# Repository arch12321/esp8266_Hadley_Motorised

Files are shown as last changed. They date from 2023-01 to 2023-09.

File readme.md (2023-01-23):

# Intro

***PLEASE NOTE MAIN VERSIONS OF MODELS AND CODE EXIST ON GITHUB ALONG WITH THE CODE AND WILL DO SO UNTIL PRINTABLES SUPPORTS PULL REQUESTS***

Welcome to my update to the metric hadley to add motorised control.  Please note that as the code (initialy VERY basic) evolves it will live on GitHub where folk who are way smarter and talented than me hopefully will make it better.  Similarly the models will exist on GitHub so that folk can improve and merge change their improvements to a single place so that there is a hopefully single best version (hopefully) and not many forks.

Once build, this will allow you to control your telescope from a webpage.   In due course the intent is to improve the code so that you can select targets and the telescope automatically moves to point at it, and will track it's position over time.  This requires a few more updates, and some coding to make work, but it's very possible.

With this, I recommend replacing the all plastic bearings with ‘proper’ bearings, this gives much smoother movement.  While it will work without this, the movement can be slightly jerky which would be a problem for small/slow movements when tracking objects in the sky.  

Anyway - firstly - the readme on github is the latest doc - pls see that for more details and code etc.

# Parts list

For hardware that needs to be purchased, you will need:

* ESP8266 Microcontroller (I used a D1 mini clone) - something like https://www.amazon.co.uk/dp/B08BTH77F3 (note, in theory you could use an ESP32, the code should be compatible, however I haven't tested it with an ESP32, so it almost certainly won't work without some bug fixing first)
* Lazy Susan Bearing - I used this one (140mm), and all the holes etc. are based this - I have no idea how standard they are - https://www.amazon.co.uk/gp/product/B00TQT9U7U/ 
* A4988 stepper motor drivers (https://www.amazon.co.uk/gp/product/B07MXXL2KW/) note - you can use the standard ULN2003 drivers, you will just need to make a couple of code tweaks and will get less torque.  The changes are commented out in the source code.  NB - I got HR4988 chips, not A4988 - these seem to work fine and I think are just cheap chinese rip offs of the real thing, so I wouldn't expect huge longevity, but so far they seem to work.
* 2 x 28BYJ-48 5V stepper motors ( https://www.amazon.co.uk/dp/B07PPKS7GZ/ ) - I had some lying around I think I got from aliexpress for about $1 each, they seem pretty universal though. Just get the 5V version
* An electrolytic capacitor (at least 100uF and >12V).  I think mine is 1000uF, but that's too big, it's just one I had a drawer full of
* 5V → 12V boost converter (10V would prob be OK too).  I used this https://www.amazon.co.uk/gp/product/B08M42BT3G/ but anything that can 0.4 A at 12V should be plenty (I measure about 95mA per motor, I have no idea how much the stepper controllers use, but they get hot..so some..) so I would estimate a total of 400mA capacity should give plenty of headroom
* 2 x 6700 bearings (2RS, ZZ - doesn't matter)
* Some solder, basic soldering skills
* A computer to flash the ESP8266 (i.e to load the computer program onto the ESP8266 microcontroller)
* USB battery pack and micro-USB wire for power
* 6mm wide closed loop GT2 timing belt - I used a 500mm one, but I think a 400mm would be OK
* 8mm M4 screws x4 (I think)
* 4 x M4 nuts
* 12mm M4 screws x16 (I think - You can get away with 8mm screws for these if needed - 8 of these hold the modified bearings (large semicircular ish things) in place - I ran out and used 8mm screws here - they are OK but 12mm better)
* 8mm M3 screws x6 (to secure the motors and bearings)
* 6mm M3 Heat set inserts x6
* 6mm M4 Heat set inserts x 12 (could use 8 here - 8 of these these connect the metric frame to the rotating base, I used 4 due to me being tighter than 2 layers of paint, there are holes for 8).  The other 4 are for the below screws.
* 16mm M4 x4 (these go through the lazy susan from the bottom into heat set inserts to hold the rotation base (the thing that deliberately looks a bit like a ship's helm) to the bearing)
* 10mm M4 Heat set inserts (could use a different size) x4.  These are to hold the bearing and ring gear to the optional base.
* Countersunk 20mm M4 screws - these connect the lazy susan to the optional base

# Circuit design

This is pretty straight forward, I just used some stripboard (approx 60mm x 60mm in size) and soldered together some breakout boards.  I wanted to have it so I could power the whole thing from a USB power bank as turny things connected to wires leads to tangles, so having an isolated power source I could put inside the turny thing seemed sensible and to provide the 5V input to drive the esp8266 board.  I therefore used a boost converter to get the required 12v ish to drive the motor (more on why I need 12V to drive 5V motors below) all powered from a 5V input.

While I haven't actually drawn the circuit properly - I have put some photos of the way I did it.  Note you probably could power this direct from the ESP8266 micro USB, I just just the separate board to put the power input in a different place.

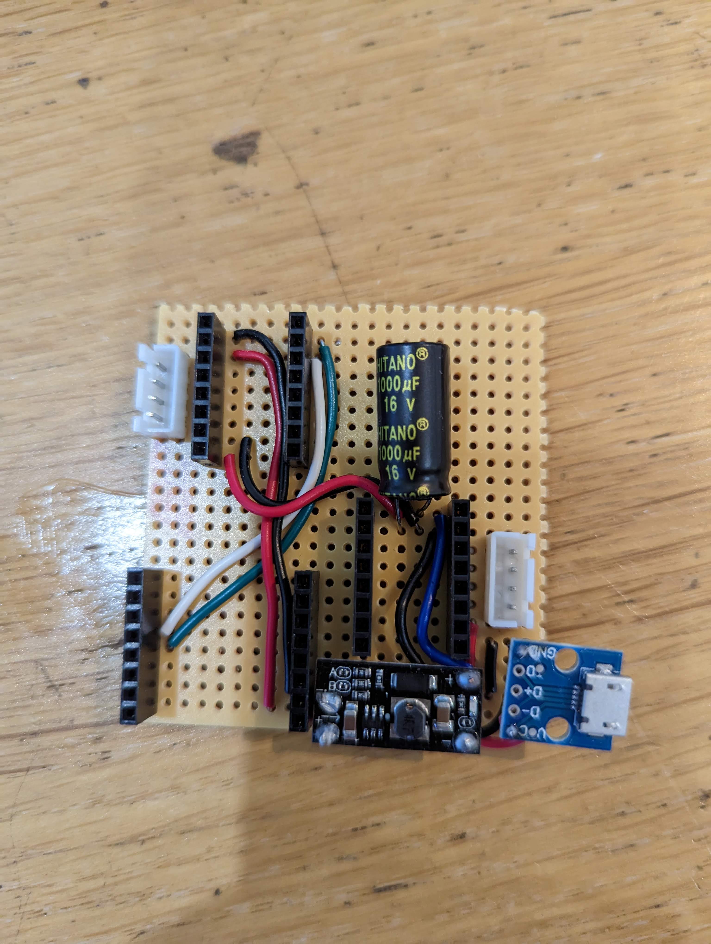
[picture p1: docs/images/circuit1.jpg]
photo of circuit1

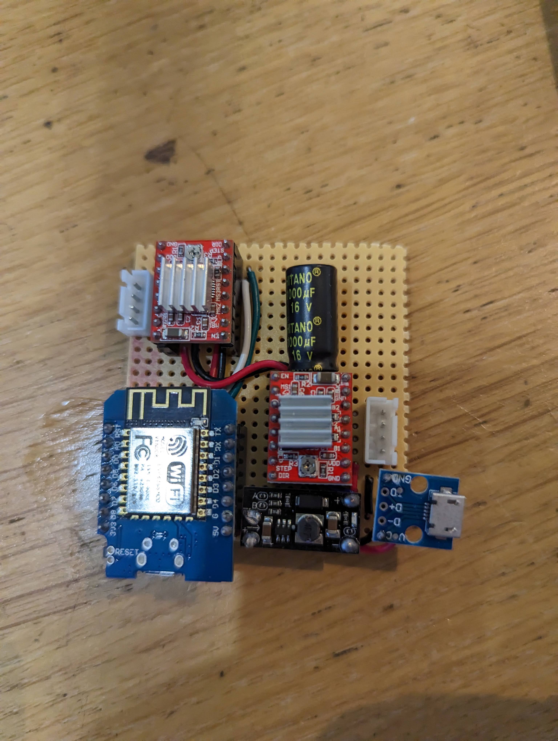
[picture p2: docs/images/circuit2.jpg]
photo of circuit2

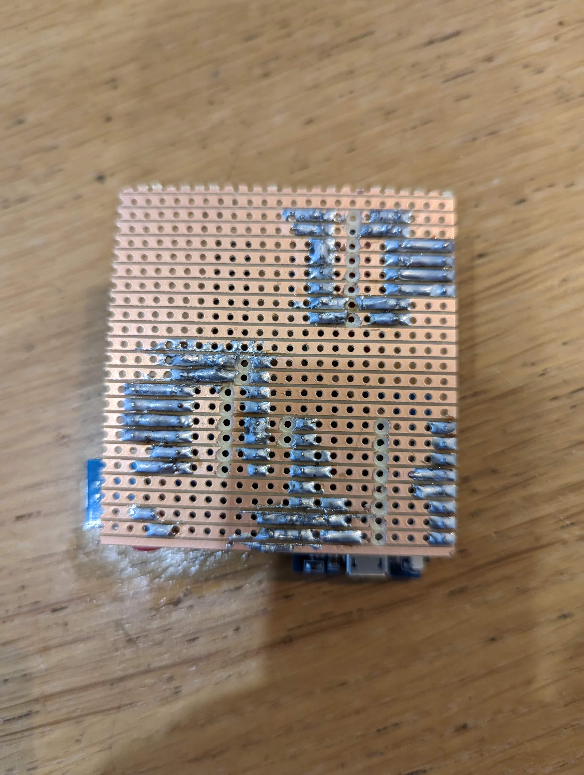
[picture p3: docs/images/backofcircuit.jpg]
photo of backofcircuit


# Stepper Driver Setup

You can use the ULN2003 driver for the 28BYJ-48 stepper motor with no modifications in unipolar mode, however various folks have noted this gives a torque of around 300-380g.cm of torque - this can be roughly doubled to 800g.cm by moving to bipolar operation (which as you move from energising 1/4 of the coils at one time in unipolar mode to energising 1/2 the coils at one time kinda makes empirical sense to me).  From my experiements, moving the steppers to bipolar operation did indeed improve performance, and while the steppers in unipolar/ULN2003 operation do move the telescope, more torque is more reliable, less likely to miss steps, and as Mr Clarkson might say, more power = better.  Given the simplicity of the modification and low cost of A4988 boards (mine are actually HR4988 boards due to dubious sales tactics calling them A4988 compatible (I missed the compatible bit) but they work fine) I decided to go for bipolar operation in this.  See https://ardufocus.com/howto/28byj-48-bipolar-hw-mod/ for details on how to do this.  The one problem I ran into was that when removing the blue plastic cover to access the PCB, a bit of the blue plastic broke off and stayed in the housing, which given there are small white plastic gears in the same area seems less than ideal.  The motor that controls elevation (up/down) is orientated such that if there is a small bit of plastic it should sit away from the plastic gears and so be OK (the gears are only one side of the motor). This however won't work for the motor that rotates the telescope, and so in one of the photos on https://www.printables.com/model/377199-motorised-mount-for-hadley-telescope oif the motor showing the motor PCB you will see I bent the side of the housing out - this was to get that super annoying bit of blue plastic out - this is easy to do with needle nosed pliars.

From the photos you will see I also removed the red wire and replaced the 5 pin JST connector with a 4 pin JST conector and sleeved the cables with white PET sleeving.  This is entirely optional and I did it both to simplify the connections to the stepper driver board, and also to assuage some of my OCD by making it look tidier overall.  The remaining niggle is I only had white sleeving, and everything else is black, which annoys me, but I think I can live with it...I think...In any case, should you decide to replace the JST connector, I recommend cutting the 5 pin plastic JST housing off the pins rather than either trying to remove the pins individually or cutting the wires and crimping on new connectors.  Having tried all 3 approaches, destroying the white plastic JST housing I found far and away the quickest and easiest approach.

The current limit of the 125mV a4988 potentiometer - gives approx 95mA measured at full step.  Equates to current limit of (1/0.7)*95 = 136mA limit as full step current is limited to 70% of max.

Note need at LEAST 47uF (I would use a min of 100uF) electrolytic capacitor to protect a4988 board from LSC voltage spikes. See https://www.pololu.com/docs/0J16/all for more details on this fascinating topic.  TL:DR? Do not use a ceramic capacitor.

# Mechanical Gearing

Note the conversion of degrees to number of steps is done in the JS file.  This is done to decouple essentially config from the ESP8266 firmware.  In due course, the intent is separate the HTML/JS/CSS files from hosting on the ESP8266 to decouple this and accelerate development, though frankly OTA updates are not hard so whether this ever gets done is low priority, especially as it's possible to update the filesystem and code over the air (OTA) over a local network.

## Horizontal
Ring gear = 82 teeth<br>
Drive gear = 10 teeth<br>
Stepper motor =-= 32*63.68395 steps per revolution = 2037.8864<br>

Therefore full revolution = (82/10)*2037.8864 = 16,710.66848 steps per 360 degrees<br>
And 1 degree = 46.41852355555556 steps<br>
Or 1 step = 0.0215431238092517 degrees<br>

https://randomnerdtutorials.com/stepper-motor-esp32-websocket/<br>

## Vertical
Big wheel 150 teeth upped to 230<br>
Drive wheel 20 teeth - (small version 12)<br>

Therefore full revolution = (230/20)*2037.8864 = 16,710.66848 steps per 360 degrees<br>
And 1 degree = 65.0991488888889 steps<br>
Or 1 step = 0.015361183933553 degrees<br>

## Summary

| Item | Turntable | Elevation |
| ---- | ---- | ---- |
| Drive Gear | 10 | 20 |
| Pulley | 82 | 230 |
| Mechanical Advantage | 8.2 | 11.5 |
| Steps per revolution (motor) | 2037.8864 | 2037.8864 |
| Steps per revolution (telescope) | 16710.66848 | 23435.6936 |
| No. of steps to move 1 degree | 46.41852356 | 65.09914889 |
| No of degrees 1 step moves | 0.021543124 | 0.015361184 |

# Flashing ESP8266 (i.e. putting the code onto the ESP8266)

If you are not familiar with flashing microcontroller, I highly recommend the Random Nerds tutorials.  This repo uses VS Code running PlatformIO, and I recommend this is what you use to flash - there is a full guide here: https://randomnerdtutorials.com/vs-code-platformio-ide-esp32-esp8266-arduino/ on how to set everything up - this can be daunting at first, but if you follow the guide, you should be fine.  Once you have VS Code setup and PlatformIO installed in VS Code just follow the steps below:

1. Clone the github repo or download the code and unzip to folder.  You should now have a folder with all the code in multiple folders and few files in the top level directory (e.g. readme.md, platformio.ini and some others)
2. Open VS Code, go to File --> Open Folder and find the folder you unzipped the files into (this folder must contain platformio.ini at the top level within it - not another folder with the platformio.ini in that)
3. Plug your ESP8266 into computer (if using an ESP32, update the platformio.ini file with your board, platform, and remove the filesystem line as you'll use SPIFFS not LITTLEFS)
4. Click the alien head in the left hand menu (platformio icon) and click Platform --> Erase Flash (just to be sure) and wait for a success message in the terminal.  Should take 15-20 seconds ish.
5. In theame menu, click Platform --> Build Filesystem Image and wait for a success message in the terminal. Should take a few seconds.
6. In the same menu, click Platform --> Upload Filesystem Image and wait for a success message in the terminal.  These steps, wipe the flash memory, then uploads the HTML, CSS and JS files in the "data" folder to the microcontroller.  Should take 10-15 seconds.
7. Click the right pointing arrow at the bottom of your screen (or click the alien head in the left hand menu --> General --> upload).  This will compile the code and then upload the binary to your microcontroller, then reset it.  This should take around 40-50 seconds.  If you now click the 2 pronged plug thing at the bottom of your screen you should get the serial messages from the microcontroller.
8. With your phone/laptop/computer/tablet open your wifi settings, and connect to the HadleyTelescope wifi network
9. If not autodirected, go to the sign-in page (192.168.4.1 by default) and click on "Configuration".  In the fist SSID box, put your wifi network name and the password in the Password field. Leave the rest blank or with default values.  Click "SAVE"
10. If you clicked the 2 pronged plug icon thing at the bottom of your screen (serial monitor terminal) you should then see a bunch more info and the local IP of your microcontroller.  If not, you can probably find it with the hostname of [http://hadleyTelescope](http://hadleyTelescope) or in your router's DHCP tables.  If you didn't click the 2 pronged plug - you can do so now, and click the reset button on your microcontroller (or unplug and plug back it back in) and you can get the local IP address.

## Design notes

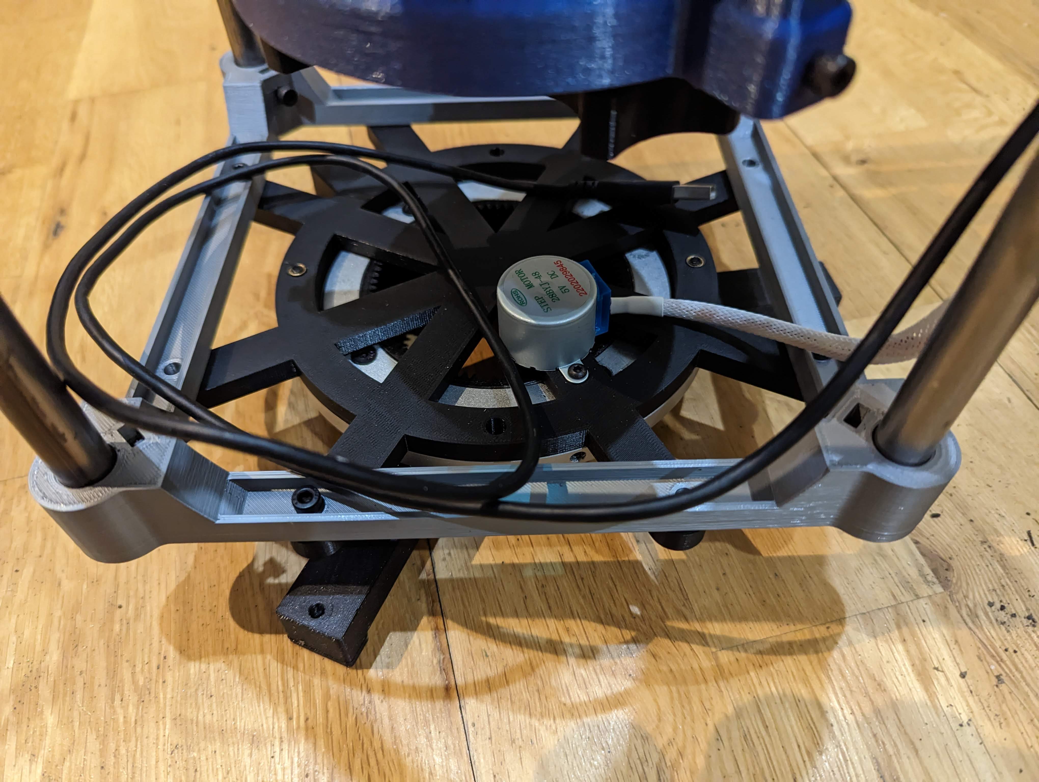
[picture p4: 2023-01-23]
docs/images/base.jpg

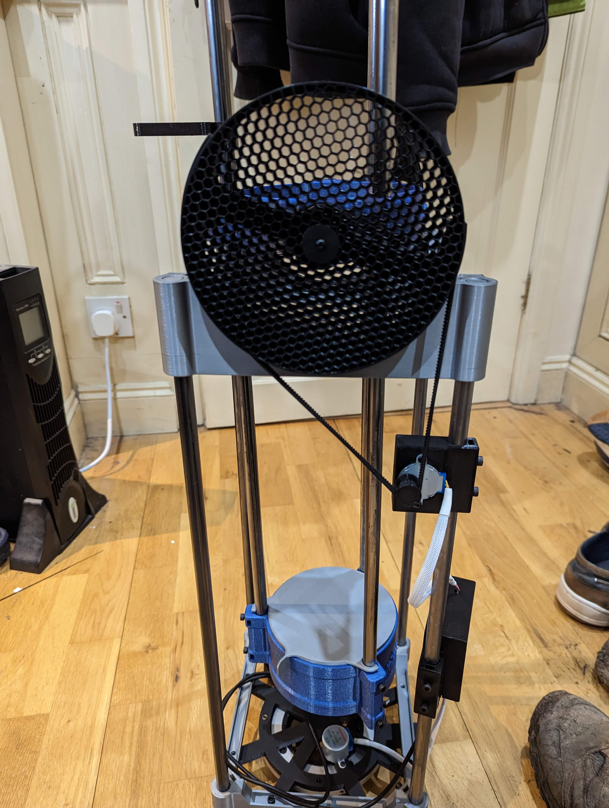
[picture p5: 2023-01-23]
docs/images/telescope.jpg

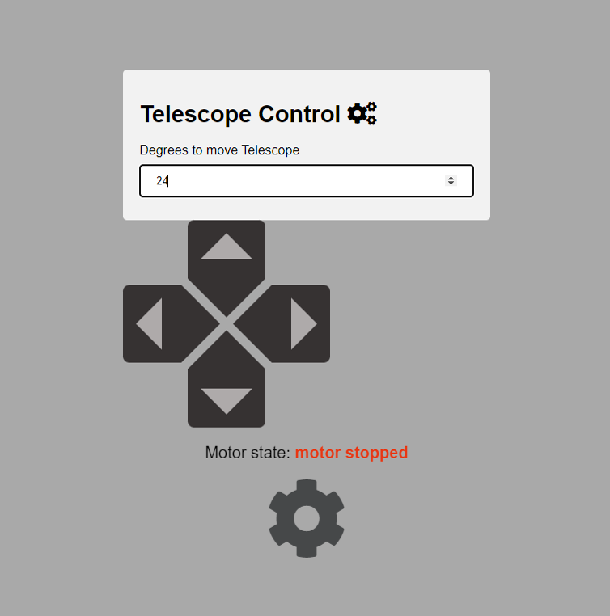
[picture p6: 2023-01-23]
docs/images/ui.png

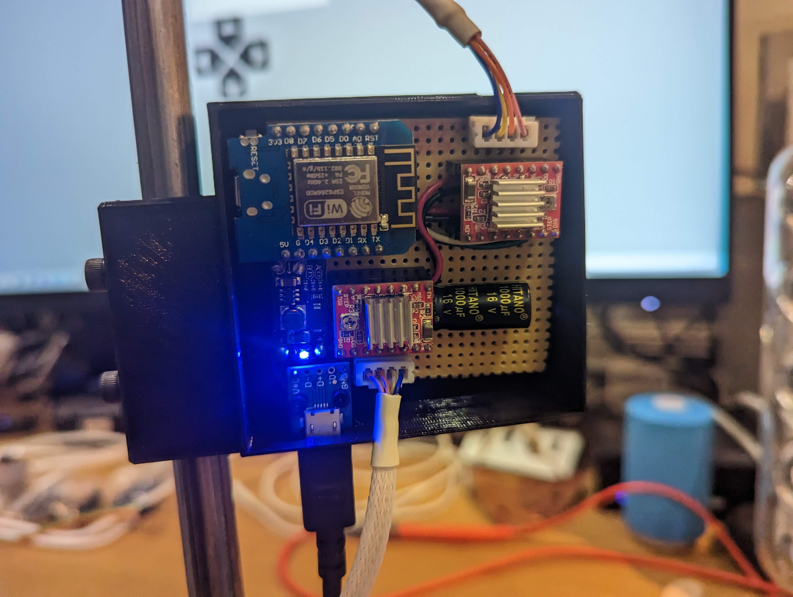
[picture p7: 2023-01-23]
docs/images/circuitinabox.jpg

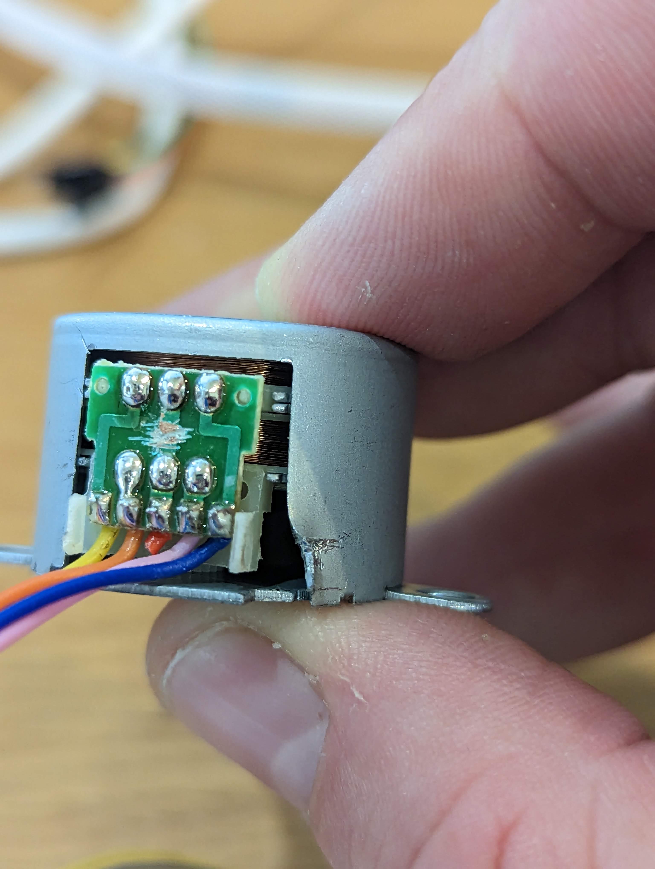
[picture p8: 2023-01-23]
docs/images/bipolarmod.jpg

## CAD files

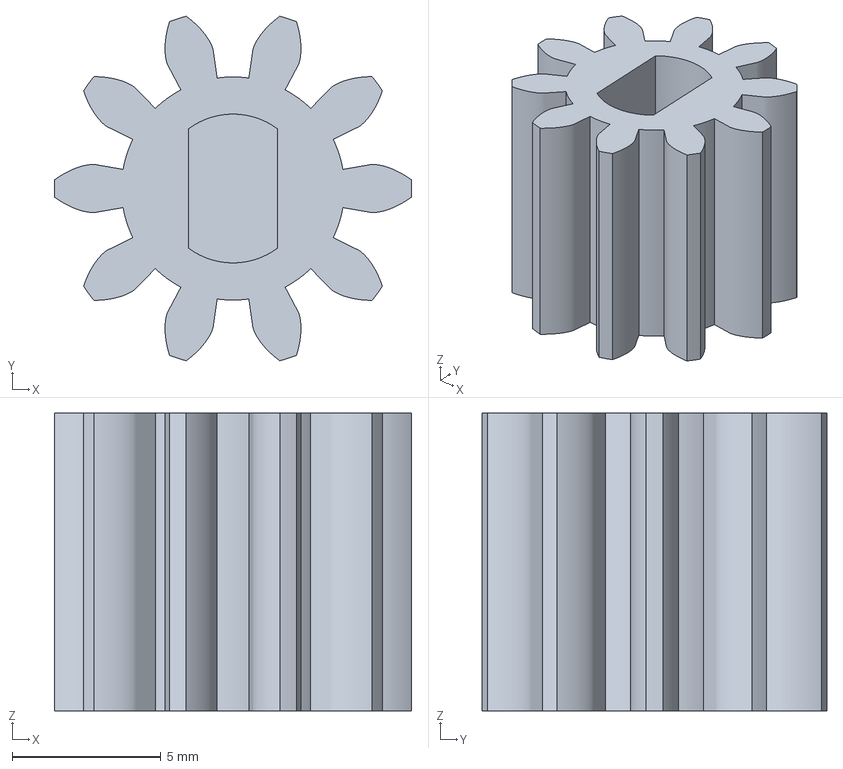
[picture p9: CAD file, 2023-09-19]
docs/10 tooth spur.3mf
12.0 x 11.6 x 10.0 mm

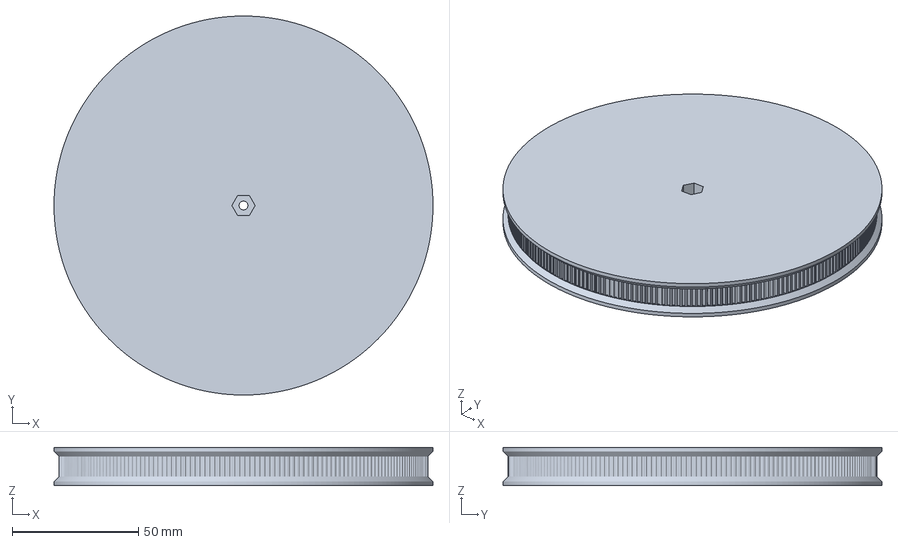
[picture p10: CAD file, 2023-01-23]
docs/Bearing mount pulley large.3mf
149.9 x 149.9 x 15.2 mm

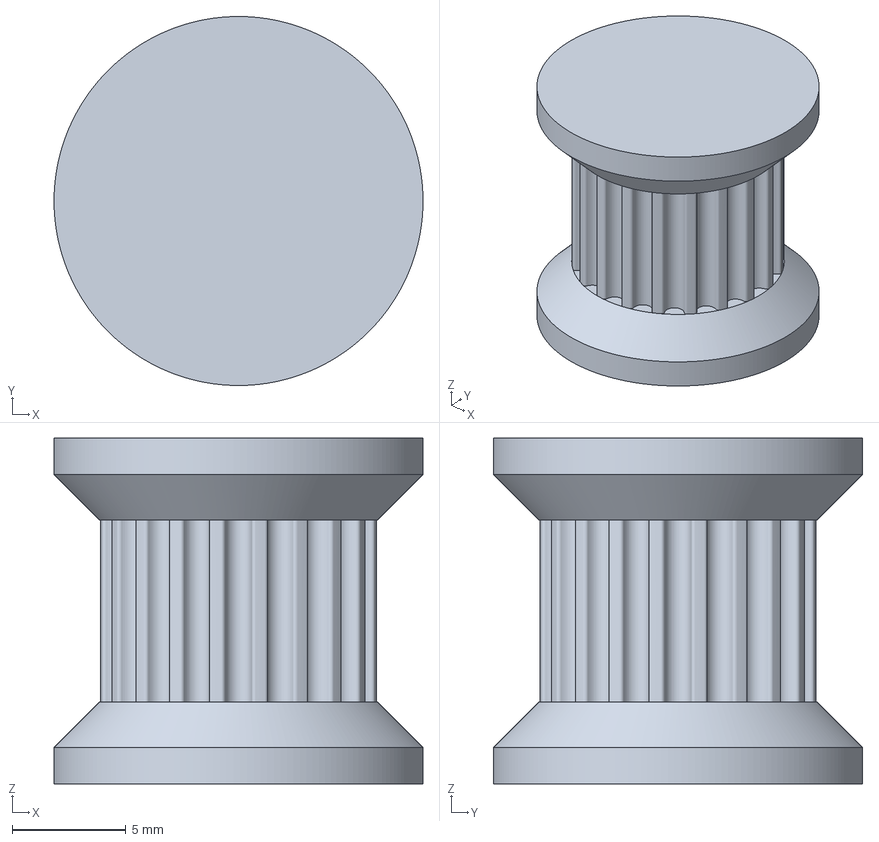
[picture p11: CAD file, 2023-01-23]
docs/GT2 drive gear.3mf
16.2 x 16.2 x 15.2 mm

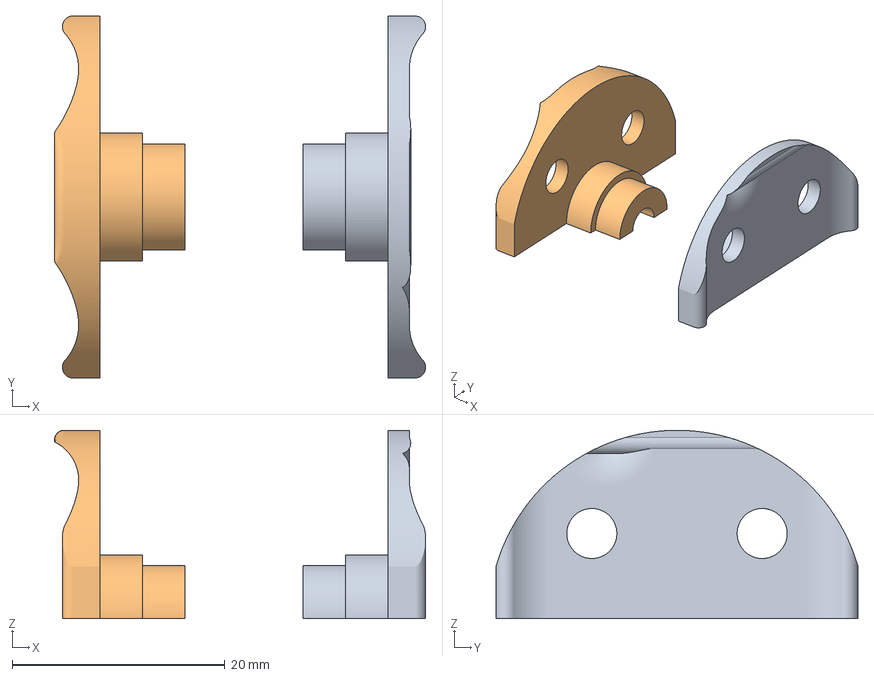
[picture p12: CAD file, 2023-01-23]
docs/Bearing Mounts - no pulley.3mf
34.9 x 34.0 x 17.7 mm
Bearing Mount 2
Bearing Mount 1

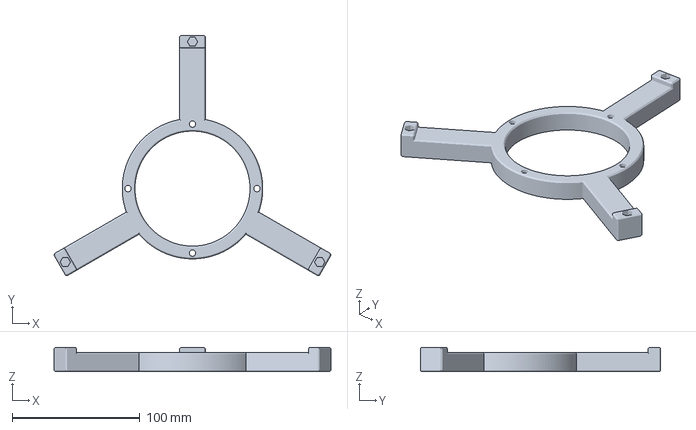
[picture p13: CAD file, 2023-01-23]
docs/base.3mf
216.8 x 188.2 x 19.0 mm

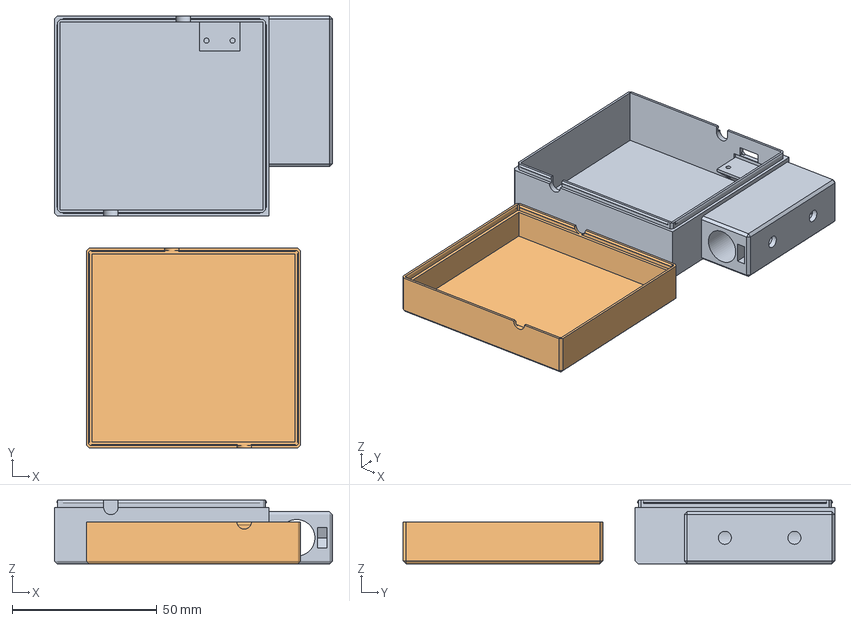
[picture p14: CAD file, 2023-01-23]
docs/electronics box v2.3mf
96.0 x 149.1 x 22.0 mm
pulley mount v6.stl_2
Electronics Box Top v2.stl

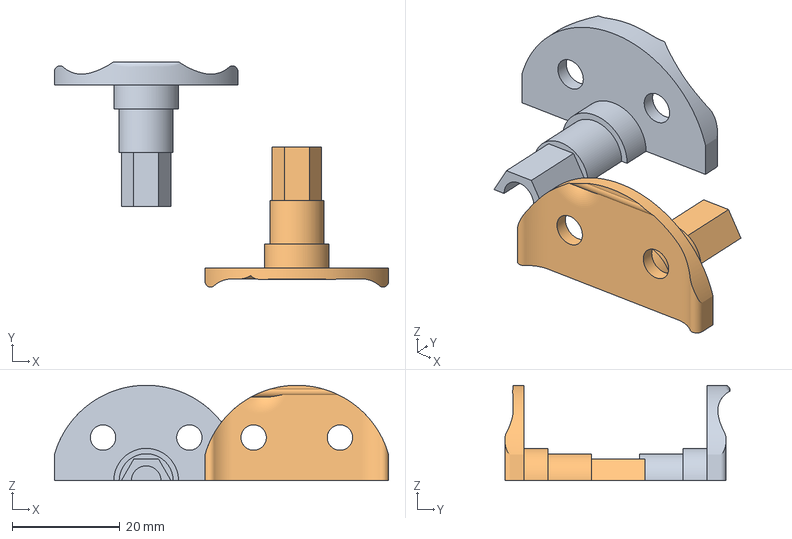
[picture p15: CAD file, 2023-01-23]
docs/Bearing Mounts.3mf
61.9 x 41.8 x 17.7 mm
Bearing Mount 1
Bearing Mount 2

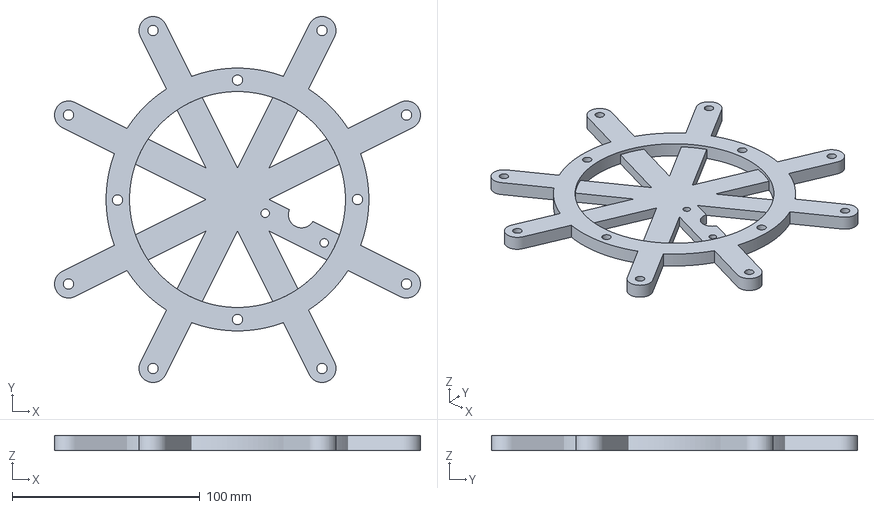
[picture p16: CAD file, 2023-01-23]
docs/rotation base.3mf
195.0 x 195.0 x 8.00 mm

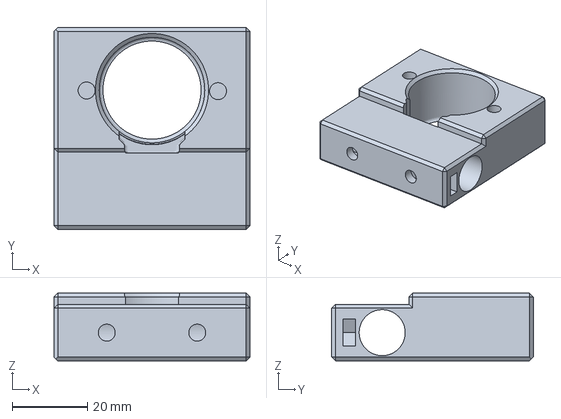
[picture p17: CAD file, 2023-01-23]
docs/Motor vertical mount.3mf
52.0 x 53.5 x 18.0 mm

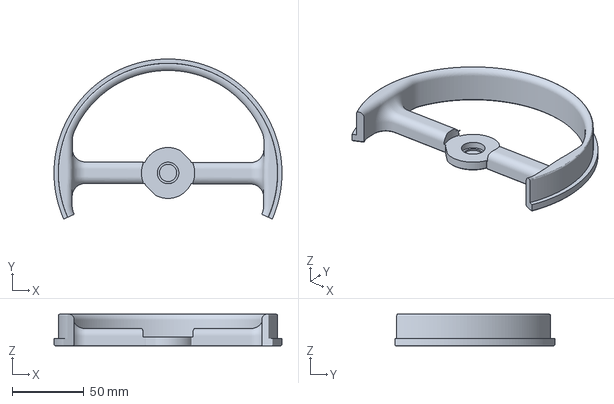
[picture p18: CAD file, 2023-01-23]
docs/Bearing mount np pulley large.3mf
158.4 x 111.1 x 22.0 mm

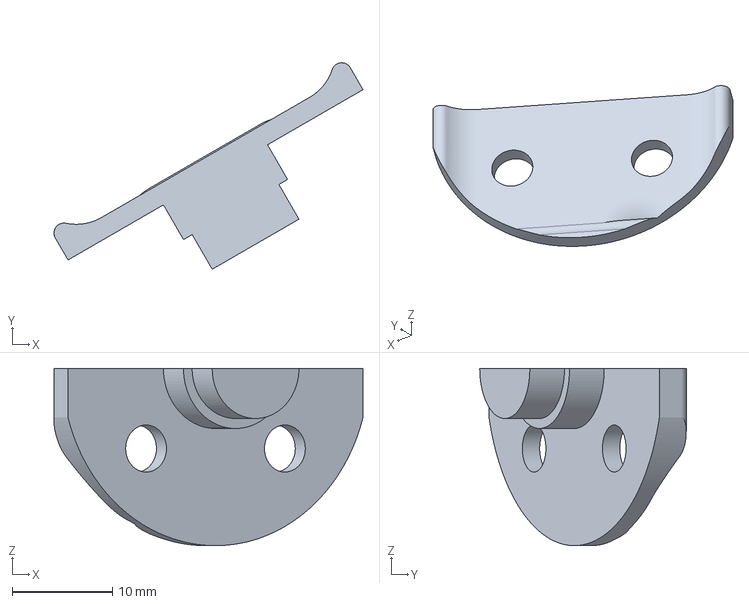
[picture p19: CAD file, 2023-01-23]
docs/Bearing Mount 2 - no pulley.3mf
30.8 x 20.6 x 17.7 mm

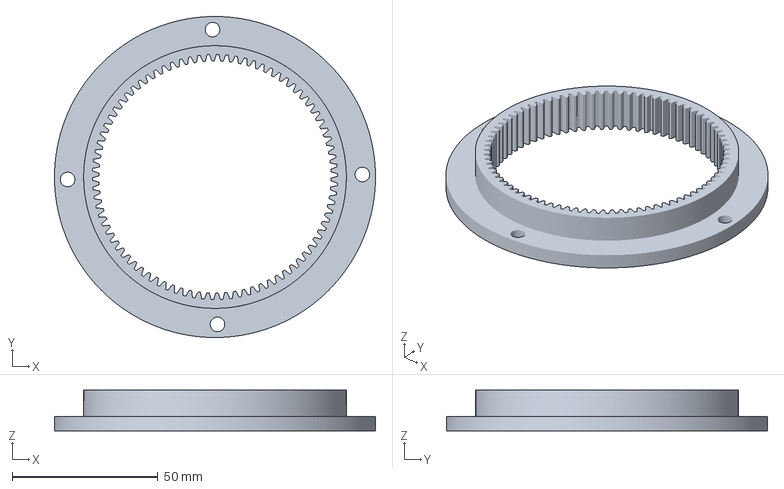
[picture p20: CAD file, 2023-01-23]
docs/Ring gear.3mf
110.0 x 110.0 x 14.0 mm

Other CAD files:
docs/Bearing for Pulley.3mf

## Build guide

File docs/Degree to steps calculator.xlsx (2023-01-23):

 | Turntable | Vertical
Drive Gear | 10 | 20
Pulley | 82 | 230
Mechanical Advantage | 8.2 | 11.5
Steps per revolution (motor) | 2037.8864 | 2037.8864
Steps per revolution (telescope) | 16710.66848 | 23435.6936
No. of steps to move 1 degree | 46.4185235556 | 65.0991488889
No of degrees 1 step moves | 0.02154312381 | 0.0153611839

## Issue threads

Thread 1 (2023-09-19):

Missing 10 tooth drive gear

Verethy-0127, 2023-09-19:
Just about got this project done, but seem to be missing the 10t drive gear for the base. Not sure if you forgot to include the STL or if this is not mentioned in the BOM?

arch12321, 2023-09-19:
Hey - thanks for building it - i have added the 10 tooth spur gear from my print files.  Pls let me know how you get on!

Closed 2023-09-19.

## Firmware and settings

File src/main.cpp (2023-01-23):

/*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
    You should have received a copy of the GNU General Public License
    along with this program.  If not, see <https://www.gnu.org/licenses/>.
*/

#define ESP_ASYNC_WIFIMANAGER_VERSION_MIN_TARGET      "ESPAsync_WiFiManager v1.15.0"
#define ESP_ASYNC_WIFIMANAGER_VERSION_MIN             1015000

// Use from 0 to 4. Higher number, more debugging messages and memory usage.
#define _ESPASYNC_WIFIMGR_LOGLEVEL_    3

// To not display stored SSIDs and PWDs on Config Portal, select false. Default is true
// Even the stored Credentials are not display, just leave them all blank to reconnect and reuse the stored Credentials 
//#define DISPLAY_STORED_CREDENTIALS_IN_CP        false

//Ported to ESP32
#ifdef ESP32
  #include <esp_wifi.h>
  #include <WiFi.h>
  #include <WiFiClient.h>

  //needed for Arduino OTA
  #include <ESPmDNS.h>

  // From v1.1.1
  #include <WiFiMulti.h>
  WiFiMulti wifiMulti;

  // LittleFS has higher priority than SPIFFS
  #if ( defined(ESP_ARDUINO_VERSION_MAJOR) && (ESP_ARDUINO_VERSION_MAJOR >= 2) )
    #define USE_LITTLEFS    true
    #define USE_SPIFFS      false
  #elif defined(ARDUINO_ESP32C3_DEV)
    // For core v1.0.6-, ESP32-C3 only supporting SPIFFS and EEPROM. To use v2.0.0+ for LittleFS
    #define USE_LITTLEFS          false
    #define USE_SPIFFS            true
  #endif

  #if USE_LITTLEFS
    // Use LittleFS
    #include "FS.h"

    // Check cores/esp32/esp_arduino_version.h and cores/esp32/core_version.h
    //#if ( ESP_ARDUINO_VERSION >= ESP_ARDUINO_VERSION_VAL(2, 0, 0) )  //(ESP_ARDUINO_VERSION_MAJOR >= 2)
    #if ( defined(ESP_ARDUINO_VERSION_MAJOR) && (ESP_ARDUINO_VERSION_MAJOR >= 2) )
      #if (_ESPASYNC_WIFIMGR_LOGLEVEL_ > 3)
        #warning Using ESP32 Core 1.0.6 or 2.0.0+
      #endif
      
      // The library has been merged into esp32 core from release 1.0.6
      #include <LittleFS.h>       // https://github.com/espressif/arduino-esp32/tree/master/libraries/LittleFS
      
      FS* filesystem =      &LittleFS;
      #define FileFS        LittleFS
      #define FS_Name       "LittleFS"
    #else
      #if (_ESPASYNC_WIFIMGR_LOGLEVEL_ > 3)
        #warning Using ESP32 Core 1.0.5-. You must install LITTLEFS library
      #endif
   
      // The library has been merged into esp32 core from release 1.0.6
      #include <LITTLEFS.h>       // https://github.com/lorol/LITTLEFS
      
      FS* filesystem =      &LITTLEFS;
      #define FileFS        LITTLEFS
      #define FS_Name       "LittleFS"
    #endif
    
  #elif USE_SPIFFS
    #include <SPIFFS.h>
    FS* filesystem =      &SPIFFS;
    #define FileFS        SPIFFS
    #define FS_Name       "SPIFFS"
  #else
    // +Use FFat
    #include <FFat.h>
    FS* filesystem =      &FFat;
    #define FileFS        FFat
    #define FS_Name       "FFat"
  #endif
  //////

  #define LED_BUILTIN       2
  #define LED_ON            HIGH
  #define LED_OFF           LOW

#else

  #include <ESP8266WiFi.h>          //https://github.com/esp8266/Arduino
  //needed for library
  #include <ESPAsyncDNSServer.h>

  //needed for Arduino OTA
  #include <ESP8266mDNS.h>

  // From v1.1.1
  #include <ESP8266WiFiMulti.h>
  ESP8266WiFiMulti wifiMulti;

  #define USE_LITTLEFS      true
  
  #if USE_LITTLEFS
    #include <LittleFS.h>
    FS* filesystem =      &LittleFS;
    #define FileFS        LittleFS
    #define FS_Name       "LittleFS"
  #else
    FS* filesystem =      &SPIFFS;
    #define FileFS        SPIFFS
    #define FS_Name       "SPIFFS"
  #endif
  //////
  
  #define ESP_getChipId()   (ESP.getChipId())
  
  #define LED_ON      LOW
  #define LED_OFF     HIGH
#endif

//Telescope control generic includes
#include <Arduino.h>
#include <ESPAsyncWebServer.h>
#include <AccelStepper.h>

//ArduinoOTA generic includes
#include <WiFiUdp.h>
#include <ArduinoOTA.h>

// SSID and PW for your Router
String Router_SSID;
String Router_Pass;

// From v1.1.1
// You only need to format the filesystem once
//#define FORMAT_FILESYSTEM       true
#define FORMAT_FILESYSTEM         false

#define MIN_AP_PASSWORD_SIZE    8

#define SSID_MAX_LEN            32
//From v1.0.10, WPA2 passwords can be up to 63 characters long.
#define PASS_MAX_LEN            64

typedef struct
{
  char wifi_ssid[SSID_MAX_LEN];
  char wifi_pw  [PASS_MAX_LEN];
}  WiFi_Credentials;

typedef struct
{
  String wifi_ssid;
  String wifi_pw;
}  WiFi_Credentials_String;

#define NUM_WIFI_CREDENTIALS      2

// Assuming max 49 chars
#define TZNAME_MAX_LEN            50
#define TIMEZONE_MAX_LEN          50

typedef struct
{
  WiFi_Credentials  WiFi_Creds [NUM_WIFI_CREDENTIALS];
  char TZ_Name[TZNAME_MAX_LEN];     // "America/Toronto"
  char TZ[TIMEZONE_MAX_LEN];        // "EST5EDT,M3.2.0,M11.1.0"
  uint16_t checksum;
} WM_Config;

WM_Config         WM_config;

#define  CONFIG_FILENAME              F("/wifi_cred.dat")
//////

// Indicates whether ESP has WiFi credentials saved from previous session, or double reset detected
bool initialConfig = false;

// Use false if you don't like to display Available Pages in Information Page of Config Portal
// Comment out or use true to display Available Pages in Information Page of Config Portal
// Must be placed before #include <ESP_WiFiManager.h>
#define USE_AVAILABLE_PAGES     true

// From v1.0.10 to permit disable/enable StaticIP configuration in Config Portal from sketch. Valid only if DHCP is used.
// You'll loose the feature of dynamically changing from DHCP to static IP, or vice versa
// You have to explicitly specify false to disable the feature.
//#define USE_STATIC_IP_CONFIG_IN_CP          false

// Use false to disable NTP config. Advisable when using Cellphone, Tablet to access Config Portal.
// See Issue 23: On Android phone ConfigPortal is unresponsive (https://github.com/khoih-prog/ESP_WiFiManager/issues/23)
#define USE_ESP_WIFIMANAGER_NTP     true

// Just use enough to save memory. On ESP8266, can cause blank ConfigPortal screen
// if using too much memory
#define USING_AFRICA        false
#define USING_AMERICA       true
#define USING_ANTARCTICA    false
#define USING_ASIA          false
#define USING_ATLANTIC      false
#define USING_AUSTRALIA     false
#define USING_EUROPE        false
#define USING_INDIAN        false
#define USING_PACIFIC       false
#define USING_ETC_GMT       false

// Use true to enable CloudFlare NTP service. System can hang if you don't have Internet access while accessing CloudFlare
// See Issue #21: CloudFlare link in the default portal (https://github.com/khoih-prog/ESP_WiFiManager/issues/21)
#define USE_CLOUDFLARE_NTP          false

// New in v1.0.11
#define USING_CORS_FEATURE          true

////////////////////////////////////////////

// Use USE_DHCP_IP == true for dynamic DHCP IP, false to use static IP which you have to change accordingly to your network
#if (defined(USE_STATIC_IP_CONFIG_IN_CP) && !USE_STATIC_IP_CONFIG_IN_CP)
  // Force DHCP to be true
  #if defined(USE_DHCP_IP)
    #undef USE_DHCP_IP
  #endif
  #define USE_DHCP_IP     true
#else
  // You can select DHCP or Static IP here
  #define USE_DHCP_IP     true
  //#define USE_DHCP_IP     false
#endif

#if ( USE_DHCP_IP )
  // Use DHCP
  
  #if (_ESPASYNC_WIFIMGR_LOGLEVEL_ > 3)
    #warning Using DHCP IP
  #endif
  
  IPAddress stationIP   = IPAddress(0, 0, 0, 0);
  IPAddress gatewayIP   = IPAddress(192, 168, 2, 1);
  IPAddress netMask     = IPAddress(255, 255, 255, 0);
  
#else
  // Use static IP
  
  #if (_ESPASYNC_WIFIMGR_LOGLEVEL_ > 3)
    #warning Using static IP
  #endif
  
  #ifdef ESP32
    IPAddress stationIP   = IPAddress(192, 168, 2, 232);
  #else
    IPAddress stationIP   = IPAddress(192, 168, 2, 186);
  #endif
  
  IPAddress gatewayIP   = IPAddress(192, 168, 2, 1);
  IPAddress netMask     = IPAddress(255, 255, 255, 0);
#endif

////////////////////////////////////////////


#define USE_CONFIGURABLE_DNS      true

IPAddress dns1IP      = gatewayIP;
IPAddress dns2IP      = IPAddress(8, 8, 8, 8);

#define USE_CUSTOM_AP_IP          false

IPAddress APStaticIP  = IPAddress(192, 168, 100, 1);
IPAddress APStaticGW  = IPAddress(192, 168, 100, 1);
IPAddress APStaticSN  = IPAddress(255, 255, 255, 0);

#include <ESPAsync_WiFiManager.h>               //https://github.com/khoih-prog/ESPAsync_WiFiManager

// Redundant, for v1.10.0 only
//#include <ESPAsync_WiFiManager-Impl.h>          //https://github.com/khoih-prog/ESPAsync_WiFiManager

#define HTTP_PORT           80

///////////////////////////////////////////
// New in v1.4.0
/******************************************
 * // Defined in ESPAsync_WiFiManager.h
typedef struct
{
  IPAddress _ap_static_ip;
  IPAddress _ap_static_gw;
  IPAddress _ap_static_sn;

}  WiFi_AP_IPConfig;

typedef struct
{
  IPAddress _sta_static_ip;
  IPAddress _sta_static_gw;
  IPAddress _sta_static_sn;
#if USE_CONFIGURABLE_DNS  
  IPAddress _sta_static_dns1;
  IPAddress _sta_static_dns2;
#endif
}  WiFi_STA_IPConfig;
******************************************/

WiFi_AP_IPConfig  WM_AP_IPconfig;
WiFi_STA_IPConfig WM_STA_IPconfig;

void initAPIPConfigStruct(WiFi_AP_IPConfig &in_WM_AP_IPconfig)
{
  in_WM_AP_IPconfig._ap_static_ip   = APStaticIP;
  in_WM_AP_IPconfig._ap_static_gw   = APStaticGW;
  in_WM_AP_IPconfig._ap_static_sn   = APStaticSN;
}

void initSTAIPConfigStruct(WiFi_STA_IPConfig &in_WM_STA_IPconfig)
{
  in_WM_STA_IPconfig._sta_static_ip   = stationIP;
  in_WM_STA_IPconfig._sta_static_gw   = gatewayIP;
  in_WM_STA_IPconfig._sta_static_sn   = netMask;
#if USE_CONFIGURABLE_DNS  
  in_WM_STA_IPconfig._sta_static_dns1 = dns1IP;
  in_WM_STA_IPconfig._sta_static_dns2 = dns2IP;
#endif
}

void displayIPConfigStruct(WiFi_STA_IPConfig in_WM_STA_IPconfig)
{
  LOGERROR3(F("stationIP ="), in_WM_STA_IPconfig._sta_static_ip, ", gatewayIP =", in_WM_STA_IPconfig._sta_static_gw);
  LOGERROR1(F("netMask ="), in_WM_STA_IPconfig._sta_static_sn);
#if USE_CONFIGURABLE_DNS
  LOGERROR3(F("dns1IP ="), in_WM_STA_IPconfig._sta_static_dns1, ", dns2IP =", in_WM_STA_IPconfig._sta_static_dns2);
#endif
}

void configWiFi(WiFi_STA_IPConfig in_WM_STA_IPconfig)
{
  #if USE_CONFIGURABLE_DNS  
    // Set static IP, Gateway, Subnetmask, DNS1 and DNS2. New in v1.0.5
    WiFi.config(in_WM_STA_IPconfig._sta_static_ip, in_WM_STA_IPconfig._sta_static_gw, in_WM_STA_IPconfig._sta_static_sn, in_WM_STA_IPconfig._sta_static_dns1, in_WM_STA_IPconfig._sta_static_dns2);  
  #else
    // Set static IP, Gateway, Subnetmask, Use auto DNS1 and DNS2.
    WiFi.config(in_WM_STA_IPconfig._sta_static_ip, in_WM_STA_IPconfig._sta_static_gw, in_WM_STA_IPconfig._sta_static_sn);
  #endif 
}

///////////////////////////////////////////

uint8_t connectMultiWiFi()
{
#if ESP32
  // For ESP32, this better be 0 to shorten the connect time.
  // For ESP32-S2/C3, must be > 500
  #if ( USING_ESP32_S2 || USING_ESP32_C3 )
    #define WIFI_MULTI_1ST_CONNECT_WAITING_MS           500L
  #else
    // For ESP32 core v1.0.6, must be >= 500
    #define WIFI_MULTI_1ST_CONNECT_WAITING_MS           800L
  #endif
#else
  // For ESP8266, this better be 2200 to enable connect the 1st time
  #define WIFI_MULTI_1ST_CONNECT_WAITING_MS             2200L
#endif

#define WIFI_MULTI_CONNECT_WAITING_MS                   500L

  uint8_t status;

  //WiFi.mode(WIFI_STA);

  LOGERROR(F("ConnectMultiWiFi with :"));

  if ( (Router_SSID != "") && (Router_Pass != "") )
  {
    LOGERROR3(F("* Flash-stored Router_SSID = "), Router_SSID, F(", Router_Pass = "), Router_Pass );
    LOGERROR3(F("* Add SSID = "), Router_SSID, F(", PW = "), Router_Pass );
    wifiMulti.addAP(Router_SSID.c_str(), Router_Pass.c_str());
  }

  for (uint8_t i = 0; i < NUM_WIFI_CREDENTIALS; i++)
  {
    // Don't permit NULL SSID and password len < MIN_AP_PASSWORD_SIZE (8)
    if ( (String(WM_config.WiFi_Creds[i].wifi_ssid) != "") && (strlen(WM_config.WiFi_Creds[i].wifi_pw) >= MIN_AP_PASSWORD_SIZE) )
    {
      LOGERROR3(F("* Additional SSID = "), WM_config.WiFi_Creds[i].wifi_ssid, F(", PW = "), WM_config.WiFi_Creds[i].wifi_pw );
    }
  }

  LOGERROR(F("Connecting MultiWifi..."));

  //WiFi.mode(WIFI_STA);

#if !USE_DHCP_IP
  // New in v1.4.0
  configWiFi(WM_STA_IPconfig);
  //////
#endif

  int i = 0;
  status = wifiMulti.run();
  delay(WIFI_MULTI_1ST_CONNECT_WAITING_MS);

  while ( ( i++ < 20 ) && ( status != WL_CONNECTED ) )
  {
    status = WiFi.status();

    if ( status == WL_CONNECTED )
      break;
    else
      delay(WIFI_MULTI_CONNECT_WAITING_MS);
  }

  if ( status == WL_CONNECTED )
  {
    LOGERROR1(F("WiFi connected after time: "), i);
    LOGERROR3(F("SSID:"), WiFi.SSID(), F(",RSSI="), WiFi.RSSI());
    LOGERROR3(F("Channel:"), WiFi.channel(), F(",IP address:"), WiFi.localIP() );
  }
  else
  {
    LOGERROR(F("WiFi not connected"));
  
#if ESP8266      
    ESP.reset();
#else
    ESP.restart();
#endif  
  }

  return status;
}

#if USE_ESP_WIFIMANAGER_NTP

void printLocalTime()
{
#if ESP8266
  static time_t now;
  
  now = time(nullptr);
  
  if ( now > 1451602800 )
  {
    Serial.print("Local Date/Time: ");
    Serial.print(ctime(&now));
  }
#else
  struct tm timeinfo;

  getLocalTime( &timeinfo );

  // Valid only if year > 2000. 
  // You can get from timeinfo : tm_year, tm_mon, tm_mday, tm_hour, tm_min, tm_sec
  if (timeinfo.tm_year > 100 )
  {
    Serial.print("Local Date/Time: ");
    Serial.print( asctime( &timeinfo ) );
  }
#endif
}

#endif

void heartBeatPrint()
{
#if USE_ESP_WIFIMANAGER_NTP
  printLocalTime();
#else
  static int num = 1;

  if (WiFi.status() == WL_CONNECTED)
    Serial.print(F("H"));        // H means connected to WiFi
  else
    Serial.print(F("F"));        // F means not connected to WiFi

  if (num == 80)
  {
    Serial.println();
    num = 1;
  }
  else if (num++ % 10 == 0)
  {
    Serial.print(F(" "));
  }
#endif  
}

void check_WiFi()
{
  if ( (WiFi.status() != WL_CONNECTED) )
  {
    Serial.println(F("\nWiFi lost. Call connectMultiWiFi in loop"));
    connectMultiWiFi();
  }
}  

void check_status()
{
  static ulong checkstatus_timeout  = 0;
  static ulong checkwifi_timeout    = 0;

  static ulong current_millis;

#define WIFICHECK_INTERVAL    1000L

#if USE_ESP_WIFIMANAGER_NTP
  #define HEARTBEAT_INTERVAL    60000L
#else
  #define HEARTBEAT_INTERVAL    10000L
#endif

  current_millis = millis();
  
  // Check WiFi every WIFICHECK_INTERVAL (1) seconds.
  if ((current_millis > checkwifi_timeout) || (checkwifi_timeout == 0))
  {
    check_WiFi();
    checkwifi_timeout = current_millis + WIFICHECK_INTERVAL;
  }

  // Print hearbeat every HEARTBEAT_INTERVAL (10) seconds.
  if ((current_millis > checkstatus_timeout) || (checkstatus_timeout == 0))
  {
    heartBeatPrint();
    checkstatus_timeout = current_millis + HEARTBEAT_INTERVAL;
  }
}

int calcChecksum(uint8_t* address, uint16_t sizeToCalc)
{
  uint16_t checkSum = 0;
  
  for (uint16_t index = 0; index < sizeToCalc; index++)
  {
    checkSum += * ( ( (byte*) address ) + index);
  }

  return checkSum;
}

bool loadConfigData()
{
  File file = FileFS.open(CONFIG_FILENAME, "r");
  LOGERROR(F("LoadWiFiCfgFile "));

  memset((void *) &WM_config,       0, sizeof(WM_config));

  // New in v1.4.0
  memset((void *) &WM_STA_IPconfig, 0, sizeof(WM_STA_IPconfig));
  //////

  if (file)
  {
    file.readBytes((char *) &WM_config,   sizeof(WM_config));

    // New in v1.4.0
    file.readBytes((char *) &WM_STA_IPconfig, sizeof(WM_STA_IPconfig));
    //////

    file.close();
    LOGERROR(F("OK"));

    if ( WM_config.checksum != calcChecksum( (uint8_t*) &WM_config, sizeof(WM_config) - sizeof(WM_config.checksum) ) )
    {
      LOGERROR(F("WM_config checksum wrong"));
      
      return false;
    }
    
    // New in v1.4.0
    displayIPConfigStruct(WM_STA_IPconfig);
    //////

    return true;
  }
  else
  {
    LOGERROR(F("failed"));

    return false;
  }
}

void saveConfigData()
{
  File file = FileFS.open(CONFIG_FILENAME, "w");
  LOGERROR(F("SaveWiFiCfgFile "));

  if (file)
  {
    WM_config.checksum = calcChecksum( (uint8_t*) &WM_config, sizeof(WM_config) - sizeof(WM_config.checksum) );
    
    file.write((uint8_t*) &WM_config, sizeof(WM_config));

    displayIPConfigStruct(WM_STA_IPconfig);

    // New in v1.4.0
    file.write((uint8_t*) &WM_STA_IPconfig, sizeof(WM_STA_IPconfig));
    //////

    file.close();
    LOGERROR(F("OK"));
  }
  else
  {
    LOGERROR(F("failed"));
  }
}

//Telescope functions here

/*  Below is only used if using the ULN2003 driver  Note this is only for 1 stepper motor - the below will need to be repeated for the 2nd and the appropriate GPIO pin numbers updated.
#define IN1 2
#define IN2 0
#define IN3 4
#define IN4 5
AccelStepper stepper(AccelStepper::HALF4WIRE, IN1, IN3, IN2, IN4);
*/

//Start of code used for A4988 driver (bipolar)
#define DIR_TTABLE 4
#define STEP_TTABLE 5
//#define MITYPE 1 - not sure what this was for - to be investigated at some point.  perhaps.

#define DIR_TSCOPE 12
#define STEP_TSCOPE 14
// #define MITYPE 1

AccelStepper ttablestepper(AccelStepper::DRIVER, STEP_TTABLE, DIR_TTABLE);
AccelStepper tscopestepper(AccelStepper::DRIVER, STEP_TSCOPE, DIR_TSCOPE);
//End of code used for A4988 driver (bipolar)

String message = "";

//Define variables for command API / to be send from webform
String direction ="STOP";
String steps;

//Variables for AccelStepper
String TtableSteps;
String TscopeSteps;

bool notifyStop = false;

// Create webservers & websocket object
AsyncWebServer server(80);
AsyncWebSocket ws("/ws");

void notifyClients(String state) {
  ws.textAll(state);
}

//Make generic for whichever motor is called
void handleWebSocketMessage(void *arg, uint8_t *data, size_t len) {
  AwsFrameInfo *info = (AwsFrameInfo*)arg;
  if (info->final && info->index == 0 && info->len == len && info->opcode == WS_TEXT) {
    data[len] = 0;
    message = (char*)data;
    steps = message.substring(0, message.indexOf("&"));
    direction = message.substring(message.indexOf("&")+1, message.length());
    Serial.print("steps");
    Serial.println(steps);
    Serial.print("direction");
    Serial.println(direction);
    notifyClients(direction);
    notifyStop = true;
    if (direction == "down"){
      Serial.print("Down");
      tscopestepper.move(-steps.toInt());
    }
    else if(direction == "up"){
      Serial.print("Up");
      tscopestepper.move(steps.toInt());
    }
    else if(direction == "left"){
      Serial.print("Left");
      ttablestepper.move(steps.toInt());
    }
    else{
      Serial.print("Right");
      ttablestepper.move(-steps.toInt());
    }
  }
}

void onEvent(AsyncWebSocket *server, AsyncWebSocketClient *client, AwsEventType type, void *arg, uint8_t *data, size_t len) {
  switch (type) {
    case WS_EVT_CONNECT:
      Serial.printf("WebSocket client #%u connected from %s\n", client->id(), client->remoteIP().toString().c_str());
      //Notify client of motor current state when it first connects
      notifyClients(direction);
      break;
    case WS_EVT_DISCONNECT:
      Serial.printf("WebSocket client #%u disconnected\n", client->id());
      break;
    case WS_EVT_DATA:
        handleWebSocketMessage(arg, data, len);
        break;
    case WS_EVT_PONG:
    case WS_EVT_ERROR:
     break;
  }
}

void initWebSocket() {
  ws.onEvent(onEvent);
  server.addHandler(&ws);
}

void initOTA() {

  // Port defaults to 8266
  // ArduinoOTA.setPort(80);

  // Hostname defaults to esp8266-[ChipID] - comment out next line to use this default
  ArduinoOTA.setHostname("hadleyTelescope");

  // No authentication by default
  // ArduinoOTA.setPassword("admin");

  // Password can be set with it's md5 value as well
  // MD5(admin) = 21232f297a57a5a743894a0e4a801fc3
  // ArduinoOTA.setPasswordHash("21232f297a57a5a743894a0e4a801fc3");

  ArduinoOTA.onStart([]() {
    String type;
    if (ArduinoOTA.getCommand() == U_FLASH) {
      type = "sketch";
    } else { // U_FS
      type = "filesystem";
    }

    // NOTE: if updating FS this would be the place to unmount FS using FS.end()
    Serial.println("Start updating " + type);
  });
  
  ArduinoOTA.onEnd([]() {
    Serial.println("\nEnd");
  });
  
  ArduinoOTA.onProgress([](unsigned int progress, unsigned int total) {
    Serial.printf("Progress: %u%%\r", (progress / (total / 100)));
  });
  
  ArduinoOTA.onError([](ota_error_t error) {
    Serial.printf("Error[%u]: ", error);
    if (error == OTA_AUTH_ERROR) {
      Serial.println("Auth Failed");
    } else if (error == OTA_BEGIN_ERROR) {
      Serial.println("Begin Failed");
    } else if (error == OTA_CONNECT_ERROR) {
      Serial.println("Connect Failed");
    } else if (error == OTA_RECEIVE_ERROR) {
      Serial.println("Receive Failed");
    } else if (error == OTA_END_ERROR) {
      Serial.println("End Failed");
    }
  });
  
  ArduinoOTA.begin();
  Serial.println("OTA Ready");
}

void setup()
{
  Serial.begin(115200);
  while (!Serial);
  delay(200);
  Serial.print("\nStarting Async_AutoConnectAP using " + String(FS_Name));
  Serial.println(" on " + String(ARDUINO_BOARD));
  Serial.println(ESP_ASYNC_WIFIMANAGER_VERSION);

#if defined(ESP_ASYNC_WIFIMANAGER_VERSION_INT)
  if (ESP_ASYNC_WIFIMANAGER_VERSION_INT < ESP_ASYNC_WIFIMANAGER_VERSION_MIN)
  {
    Serial.print("Warning. Must use this example on Version later than : ");
    Serial.println(ESP_ASYNC_WIFIMANAGER_VERSION_MIN_TARGET);
  }
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
void loop()
{ 
  // put your main code here, to run repeatedly
  check_status();
  ArduinoOTA.handle();
  if (tscopestepper.distanceToGo() == 0 && ttablestepper.distanceToGo() == 0 && notifyStop == true){  
    direction = "stop";
    notifyClients(direction);
    notifyStop = false;
  }
  
  ws.cleanupClients();
  ttablestepper.run();
  tscopestepper.run();
}

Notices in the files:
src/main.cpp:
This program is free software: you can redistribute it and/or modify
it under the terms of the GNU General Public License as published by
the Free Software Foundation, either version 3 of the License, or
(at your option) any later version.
